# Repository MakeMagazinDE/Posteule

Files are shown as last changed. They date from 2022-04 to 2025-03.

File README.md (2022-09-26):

GitHub Logo

Maker Media GmbH
*** 

# Die animatronische Posteule

### Wie durch Zauberhand: Der Raspberry Pi verwandelt eine Plüscheule in eure persönliche kleine Mitteilungszentrale. Sie flattert, schnattert, blinzelt und kann ihren Kopf drehen. Und das beste: Ihr habt dank Python die Programmierung selbst in der Hand. 

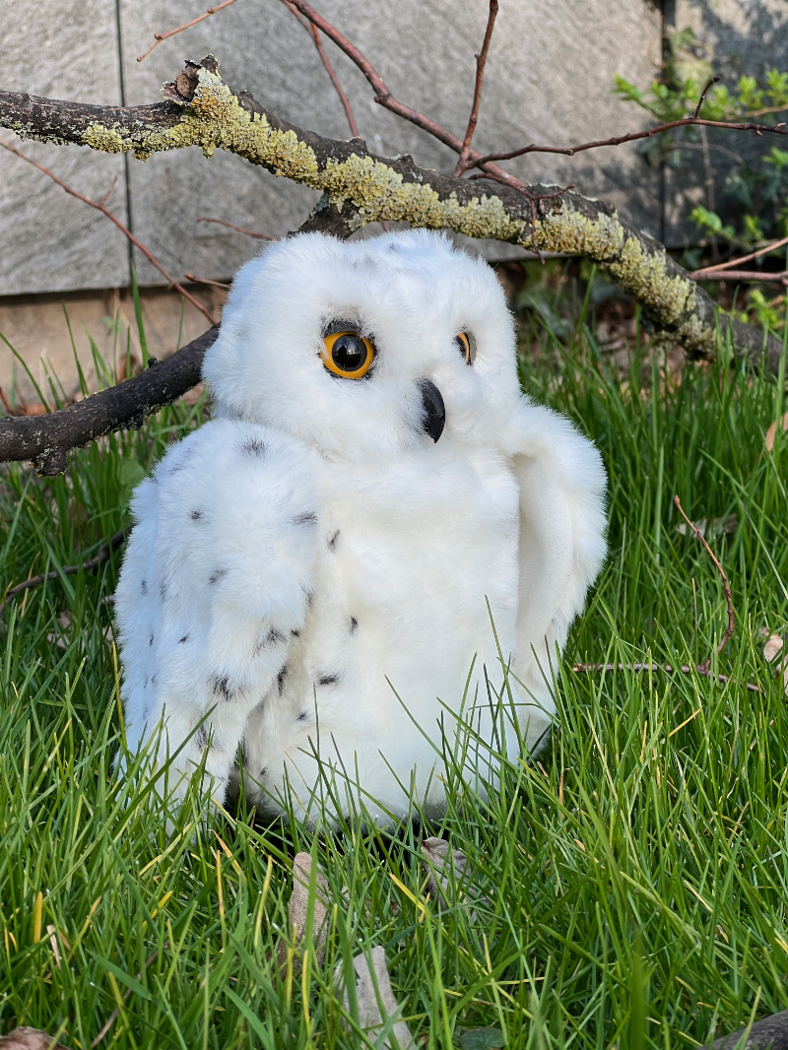
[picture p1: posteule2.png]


Hier findet ihr die benötigten Dateien für den 3D-Druck und die Skripts für die Programmierung. <br>Die 3D-Dateien sind bereits ausgerichtet und mit Cura getestet. 

### Verwendete Druckparameter:
<b>Material:</b> PLA <br>
<b>Temp.:</b> 210°C <br>
<b>Infill:</b> 25% <br>
<b>Support:</b> überall, Zickzack <br>
<b>Schichthöhe:</b> 0,2mm (0,1mm für K5, K6 und K7) <br>
<b>Druckgeschwindigkeit:</b> 50mm/s (20mm/s für K5, B1 und B2) <br>
<b>Bewegungsgeschwindigkeit:</b> 100mm/s (50mm/s für K5, B1 und B2) <br>
<b>Druckplattenhaftung:</b> Skirt (Brim für K5, B1 und B2) <br>
<br>
### Hinweise: 
### Zur E-Mail-Abfrage:
- Verwendet für die Eule eine gesonderte E-Mail-Adresse, weil die Funktion checkIncoming() nach dem Abfragen alle E-Mails löscht.
### Zu den 3D-Dateien aus Teil 1:
- Das Augenlid <b>K5</b> muss zweimal gedruckt werden, die Ringe <b>F1</b> dreimal. <br>
### Zu den 3D-Dateien aus Teil 2:
- Folgende Dateien müssen zweimal gedruckt werden: <b>A8, A9, BN1, BN3, FX</b> und <b>G4</b>
### Zu optimierten 3D-Dateien:
- Es gibt ein paar angepasste 3D-Druckdaten zu <a href="https://github.com/MakeMagazinDE/Posteule/tree/main/3D-Druck/Teil%201/Optimierte%20Modelle"><b>Teil 1</b></a> und <a href="https://github.com/MakeMagazinDE/Posteule/tree/main/3D-Druck/Teil%202/Optimierte%20Modelle"><b>Teil 2</b></a>.
### Die Grafiken 7 und 10 aus der zweiten Bauanleitung (Make 2/22) wurden mit Ziffern ergänzt:
- Ihr findet sie in dem Ordner <a href="https://github.com/MakeMagazinDE/Posteule/tree/main/Extras"><b>Extras</b></a>.

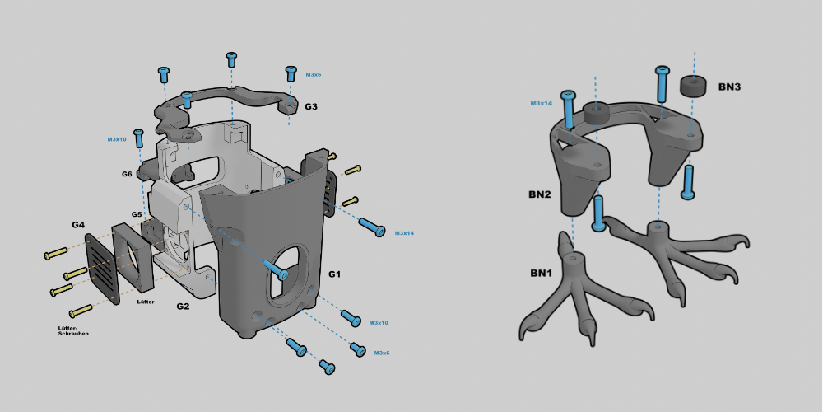
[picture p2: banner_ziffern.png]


<br>

### Hinweis zu dem Servo, der den Augenmechanismus steuert:
Die Bauform der MG90s-Servos scheint sich je nach Hersteller zu unterscheiden. Dadurch kann es passieren, dass der Arm <b>A2</b> mit <b>K1</b> kollidiert, wenn die Welle zu kurz ist oder zu weit hinten sitzt. Zwischen <b>A2</b> und <b>K1</b> sollte eine ca. 0,6mm große Lücke vorhanden sein, damit sich der Arm am Servo problemlos bewegen kann. Haltet am besten den Arm <b>A2</b> einmal an den Servo, und schaut von oben, ob ihr eine Lücke seht. <br>In dem Ordner <a href="https://github.com/MakeMagazinDE/Posteule/tree/main/3D-Druck/Teil%202/Extra"><b>3D-Druck/Teil 2/Extra</b></a> findet ihr die Datei <b>servo_spacer.stl</b>. Dabei handelt es sich um einen kleinen Ring, der in den Arm <b>A2</b> eingesetzt werden kann, bevor ihr ihn am Servo montiert. Er ist 1mm hoch, damit ihr ihn in eurem Slicer auf die richtige Größe (Z-Achse) skalieren könnt. Für alle, die bereits die Teile für den zweiten Artikel gedruckt haben: Der Abstandhalter kann auch aus Pappe gefertigt werden. In der Kurzinfo zum zweiten Artikel findet ihr den Link zu einem Video, das näher darauf eingeht.
<br>
<br>
### Befehle, die nach der Installation von Raspberry Pi OS eingegeben werden müssen <br>(siehe Teil 2 der Bauanleitung):
sudo apt update <br>
sudo apt full-upgrade <br>
sudo apt install python3-pip <br>
sudo apt install ffmpeg libavcodec-extra <br>
sudo apt install i2c-tools <br>
sudo apt install libportaudio2 <br>
sudo pip3 install imapclient <br>
sudo pip3 install smbus <br>
sudo pip3 install adafruit-circuitpython-lis3dh <br>
sudo pip3 install adafruit-circuitpython-servokit <br>
sudo pip3 install pysinewave <br>
sudo pip3 install pydub <br>

<br><br>
Den vollständigen Artikel für den <b>ersten Teil</b> der Bauanleitung gibt es in der [Make-Ausgabe 1/2022](https://www.heise.de/select/make/2022/1/2135511401796522217) zu lesen. 
<br>
Den vollständigen Artikel für den <b>zweiten Teil</b> der Bauanleitung gibt es in der [Make-Ausgabe 2/2022](https://www.heise.de/select/make/2022/2/2203916022634105772) zu lesen.

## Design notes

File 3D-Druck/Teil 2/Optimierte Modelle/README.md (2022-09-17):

In diesem Ordner befinden sich optimierte Druck-Dateien.

- <b>G2_ver2.stl</b> hat kleinere Durchgangslöcher. Ihr Durchmesser wurde von 3mm auf 2,8mm verkleinert.

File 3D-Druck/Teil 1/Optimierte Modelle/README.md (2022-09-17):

In diesem Ordner befinden sich optimierte Druck-Dateien.

- <b>N1_ver2.stl</b> benötigt keine Stützkonstruktion mehr für den 3D-Druck und verfügt über ein zusätzliches Loch, um mit <b>N2</b> verbunden zu werden.
- <b>N2_ver2.stl</b> benötigt keine Stützkonstruktion mehr für den 3D-Druck.
- <b>V1_ver2.stl</b> hat engere Löcher an den Stellen, an denen die Servos angeschraubt werden.

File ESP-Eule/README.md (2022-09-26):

GitHub Logo

Maker Media GmbH
*** 

# Die animatronische Posteule - ESP-Version

### Ob mit Plüsch oder ohne: Die animatronische Posteule aus der Make 1/22 und 2/22 läuft jetzt auch mit einem ESP32 und dem YX5300-MP3-Player. Kein Problem also, wenn ihr keinen Raspberry Pi zur Hand habt. 

Hier findet ihr die benötigten Dateien für den 3D-Druck und die Skripts für die Programmierung mit der Arduino-IDE. 

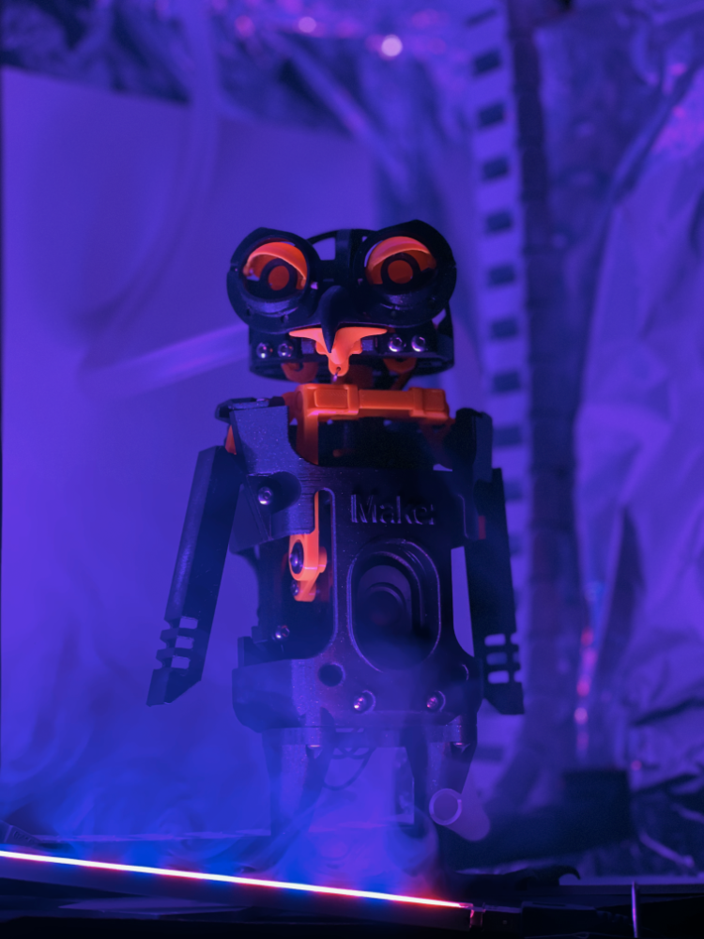
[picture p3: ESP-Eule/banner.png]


### Hinweise: 
- Ihr benötigt zusätzlich die Bauteile und Anleitungen aus der Make 1/22 und 2/22.
- Verwendet für die Eule eine gesonderte E-Mail-Adresse, weil die Funktion checkIncoming() nach dem Abfragen alle E-Mails löscht.

<br>

Den <b>ergänzenden Artikel</b> für den ESP-Umbau gibt es in der [Make-Ausgabe 5/22](https://www.heise.de/select/make/2022/5/2220807460904208992) zu lesen.
<br>
Den vollständigen Artikel für den <b>ersten Teil</b> der Bauanleitung gibt es in der [Make-Ausgabe 1/22](https://www.heise.de/select/make/2022/1/2135511401796522217) zu lesen. 
<br>
Den vollständigen Artikel für den <b>zweiten Teil</b> der Bauanleitung gibt es in der [Make-Ausgabe 2/22](https://www.heise.de/select/make/2022/2/2203916022634105772) zu lesen.

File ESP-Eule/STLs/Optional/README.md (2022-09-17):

Dieser Ordner beinhaltet optionale 3D-Modelle für die Variante der <b>[Make 5/22](https://www.heise.de/select/make/2022/5/2220807460904208992)</b>, die auch auf der <b>[Maker Faire 2022](https://maker-faire.de)</b> zu sehen war. Die ESP-Posteule lässt sich allerdings auch in der Plüsch-Variante bauen. Dafür benötigt ihr die 3D-Daten aus dem ersten und zweiten Teil der Anleitung.

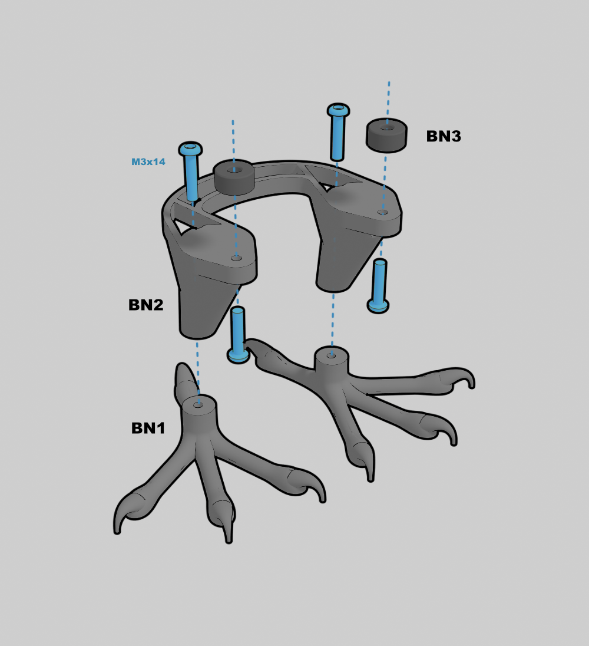
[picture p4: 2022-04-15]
Extras/posteule_grafik10_beziffert.png

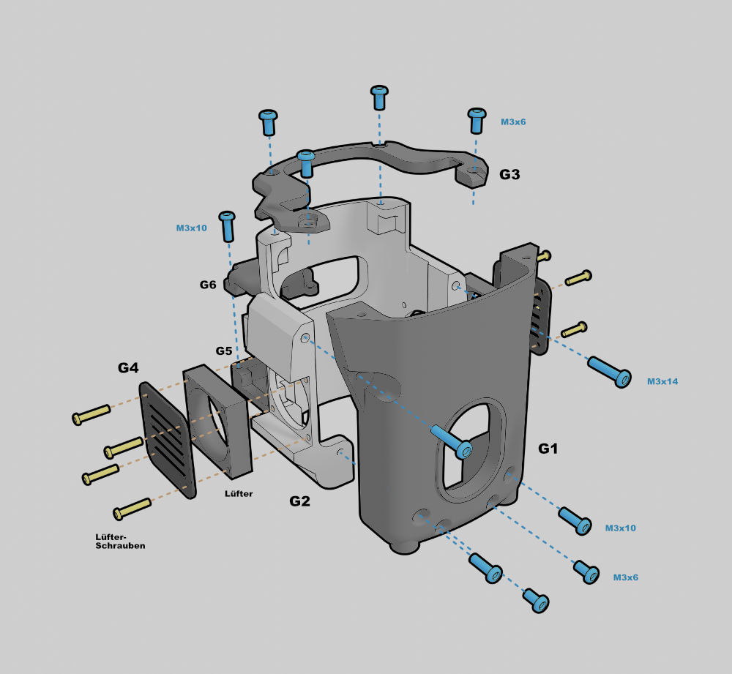
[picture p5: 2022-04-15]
Extras/posteule_grafik7_beziffert.png

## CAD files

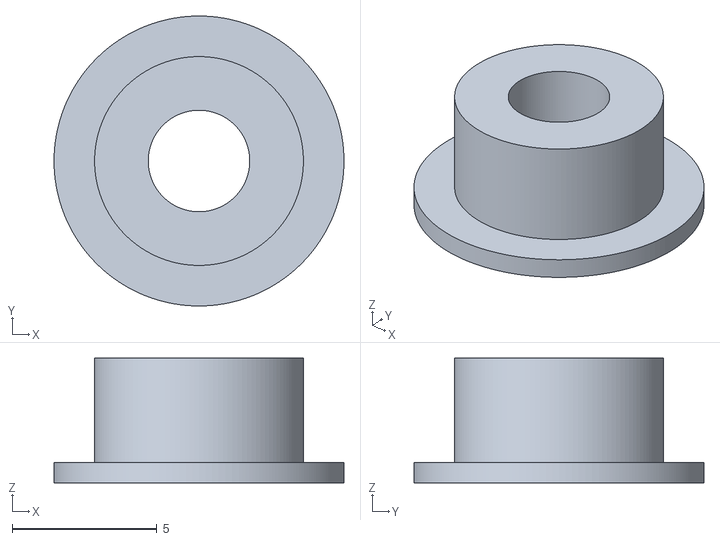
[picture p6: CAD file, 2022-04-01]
3D-Druck/Teil 1/B4.stl
10.0 x 10.0 x 4.30

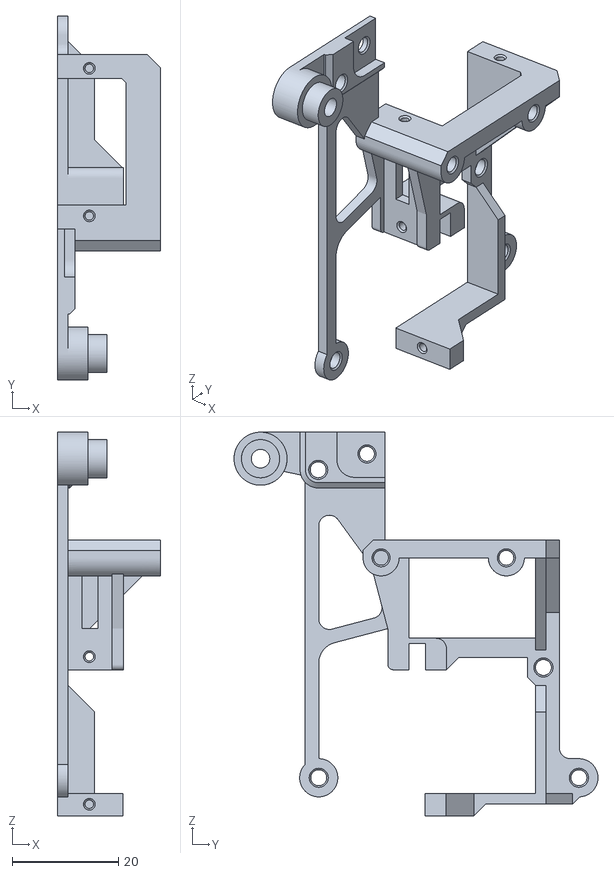
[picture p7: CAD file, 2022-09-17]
3D-Druck/Teil 1/Optimierte Modelle/V1_ver2.stl
19.4 x 68.6 x 72.3

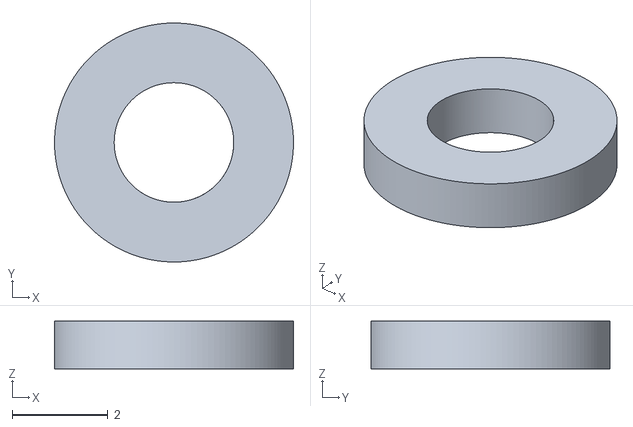
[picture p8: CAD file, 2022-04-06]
3D-Druck/Teil 2/Extra/servo_spacer.stl
5.00 x 5.00 x 1.00

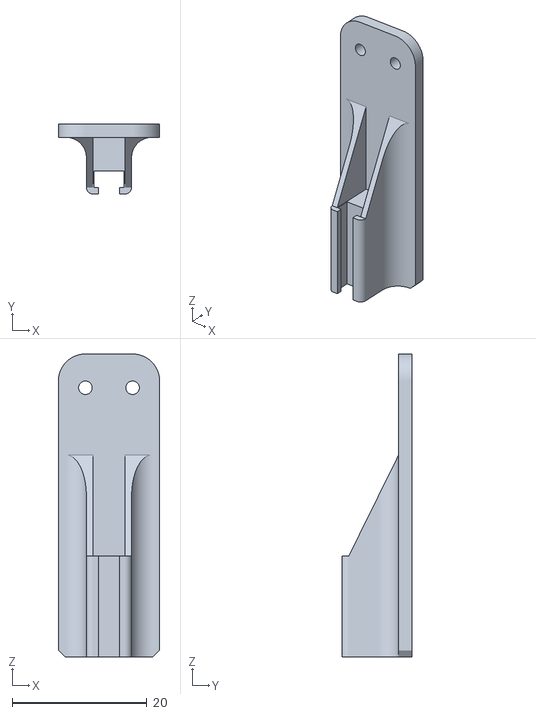
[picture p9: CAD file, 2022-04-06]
3D-Druck/Teil 2/FX.stl
15.0 x 10.4 x 44.9

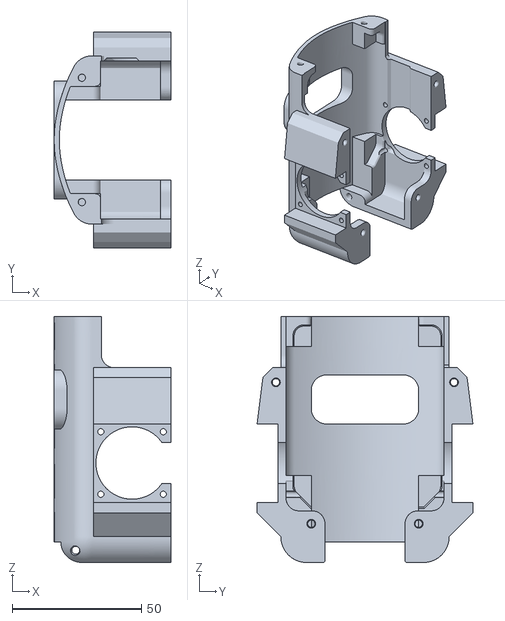
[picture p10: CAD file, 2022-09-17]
3D-Druck/Teil 2/Optimierte Modelle/G2_ver2.stl
45.2 x 83.6 x 95.3

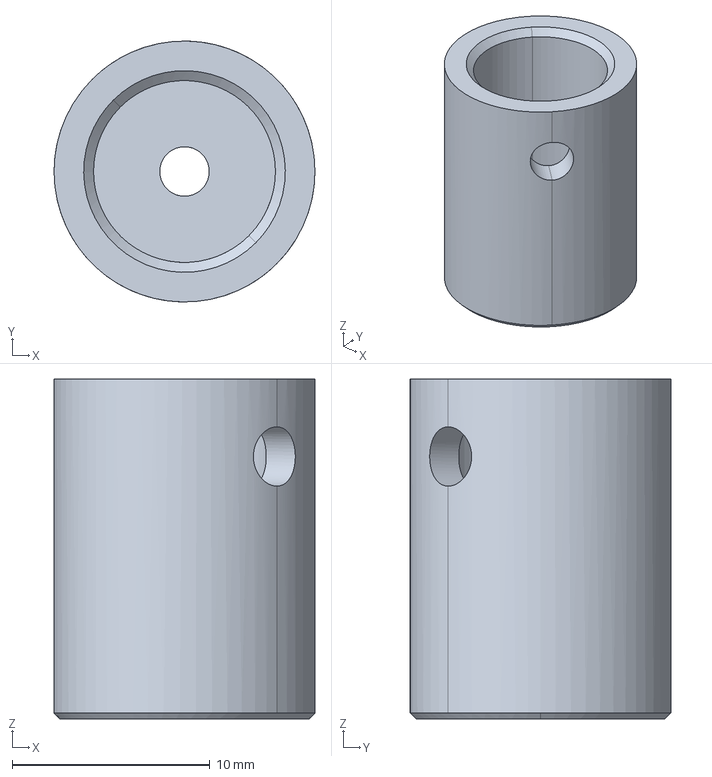
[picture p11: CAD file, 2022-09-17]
ESP-Eule/Servoverbinder-CAD/N2.stp
13.2 x 13.2 x 17.2 mm

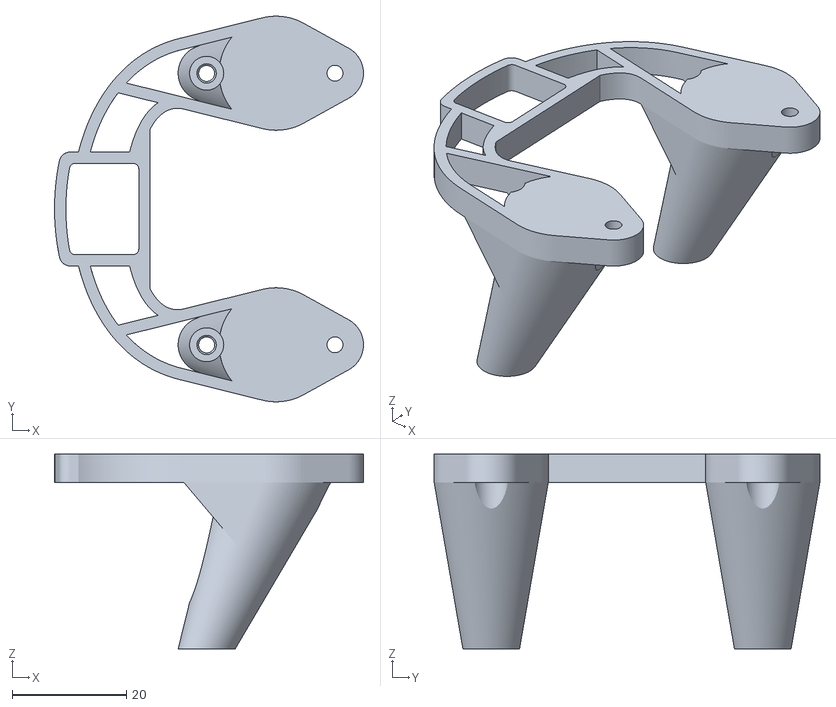
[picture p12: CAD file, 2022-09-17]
ESP-Eule/STLs/Essentials/BN2E.stl
54.2 x 67.6 x 34.2

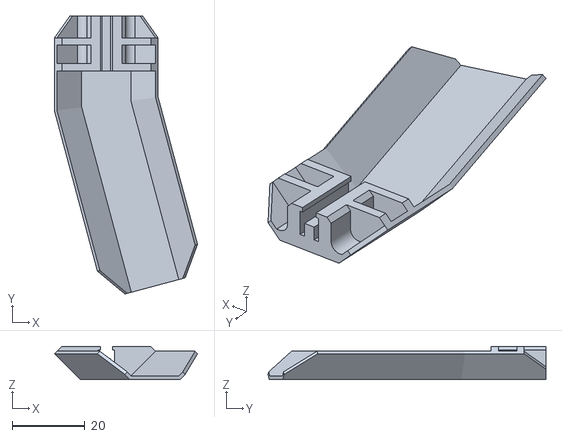
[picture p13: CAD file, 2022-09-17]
ESP-Eule/STLs/Optional/FXE_rechts.stl
39.3 x 76.2 x 9.10

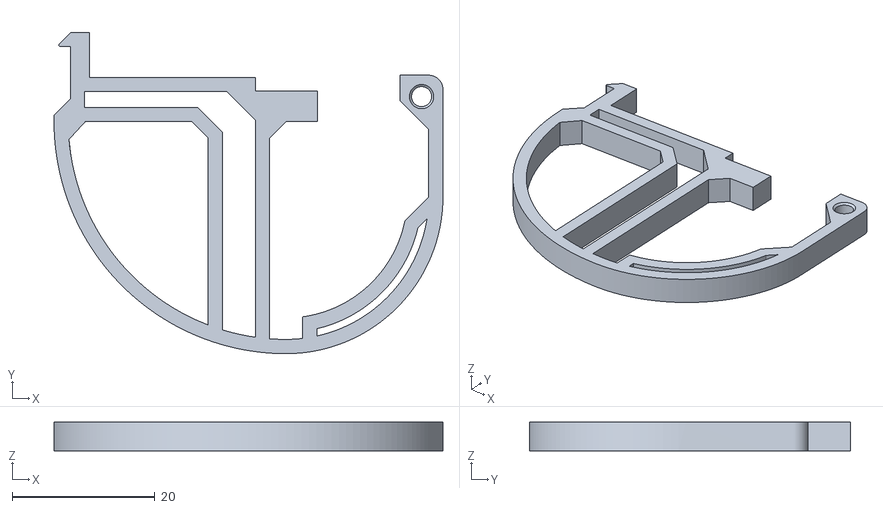
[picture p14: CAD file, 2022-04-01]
3D-Druck/Teil 1/K3.stl
54.5 x 45.0 x 4.00

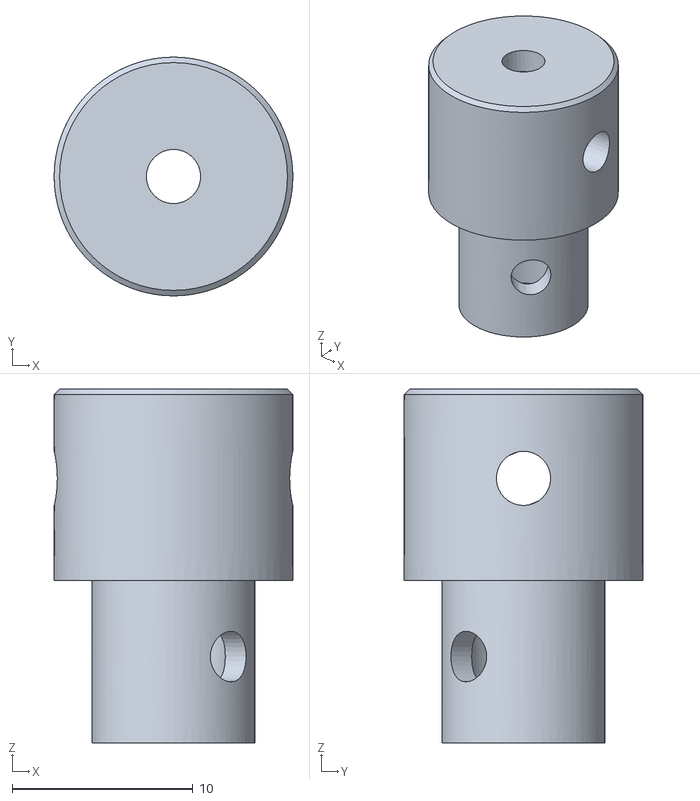
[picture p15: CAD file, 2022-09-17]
3D-Druck/Teil 1/Optimierte Modelle/N1_ver2.stl
13.2 x 13.2 x 19.6

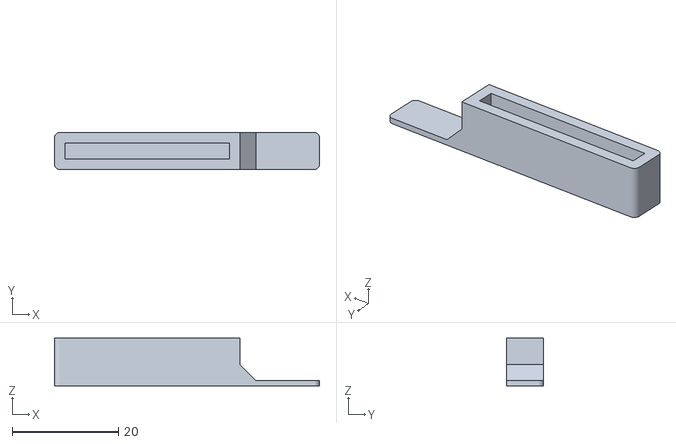
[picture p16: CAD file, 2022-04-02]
3D-Druck/Teil 2/gpio_cap.stl
50.0 x 7.00 x 9.00

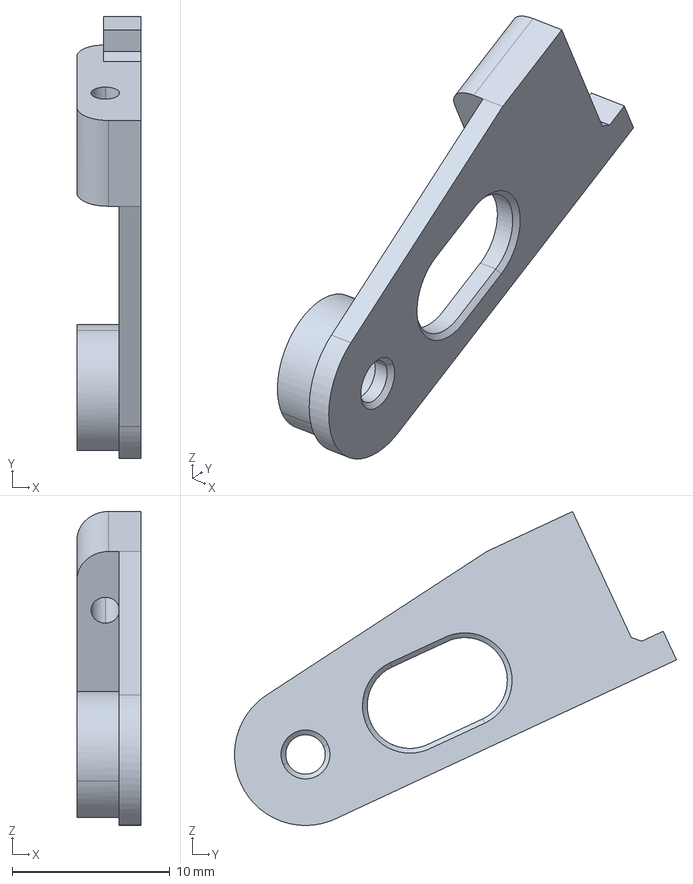
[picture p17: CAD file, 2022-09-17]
ESP-Eule/Servoverbinder-CAD/A2.stp
4.07 x 28.0 x 19.9 mm

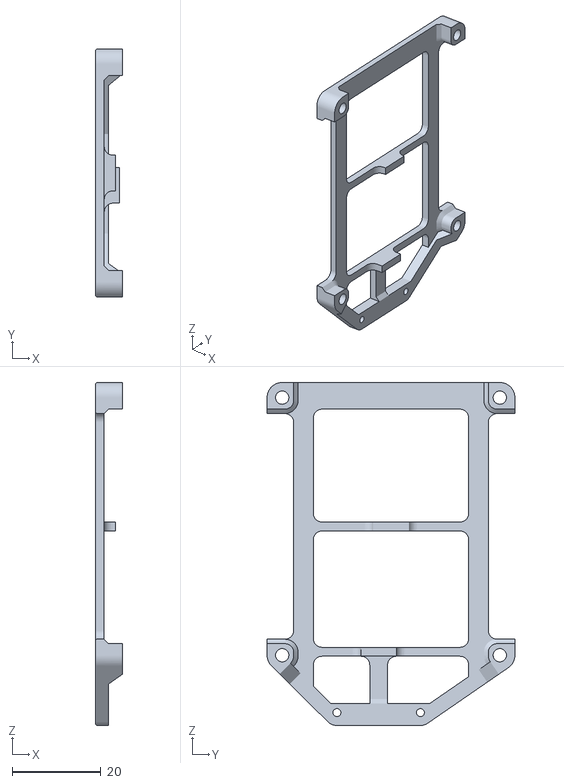
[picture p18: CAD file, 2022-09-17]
ESP-Eule/STLs/Essentials/R1E.stl
6.16 x 55.8 x 77.2

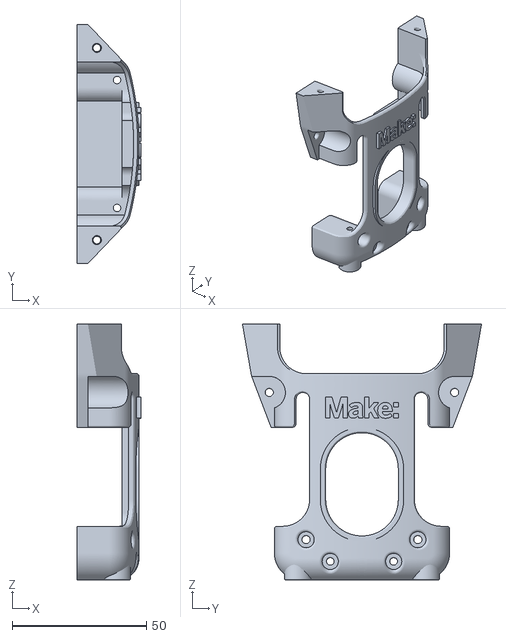
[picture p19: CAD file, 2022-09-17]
ESP-Eule/STLs/Optional/G1_cyber.stl
23.7 x 89.0 x 95.3

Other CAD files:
3D-Druck/Teil 1/Optimierte Modelle/N2_ver2.stl
3D-Druck/Teil 1/RF1.stl
3D-Druck/Teil 2/A9.stl
ESP-Eule/Servoverbinder-CAD/B5.stp
3D-Druck/Teil 1/B1.stl
3D-Druck/Teil 1/B2.stl
3D-Druck/Teil 1/B3.stl
3D-Druck/Teil 1/B5.stl
3D-Druck/Teil 1/B6.stl
3D-Druck/Teil 1/F1.stl
3D-Druck/Teil 1/K1.stl
3D-Druck/Teil 1/K2.stl
3D-Druck/Teil 1/K4_L.stl
3D-Druck/Teil 1/K4_R.stl
3D-Druck/Teil 1/K6.stl
3D-Druck/Teil 1/K7.stl
3D-Druck/Teil 1/K8.stl
3D-Druck/Teil 1/K9_L.stl
3D-Druck/Teil 1/K9_R.stl
3D-Druck/Teil 1/LF1.stl
3D-Druck/Teil 1/LF2.stl
3D-Druck/Teil 1/N1.stl
3D-Druck/Teil 1/N2.stl
3D-Druck/Teil 1/R1.stl
3D-Druck/Teil 1/R2.stl
3D-Druck/Teil 1/V1.stl
3D-Druck/Teil 1/V2.stl
3D-Druck/Teil 1/V3.stl
3D-Druck/Teil 1/V4.stl
3D-Druck/Teil 1/V5.stl
3D-Druck/Teil 2/A1.stl
3D-Druck/Teil 2/A2.stl
3D-Druck/Teil 2/A3.stl
3D-Druck/Teil 2/A4.stl
3D-Druck/Teil 2/A5.stl
3D-Druck/Teil 2/A6.stl
3D-Druck/Teil 2/A7.stl
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

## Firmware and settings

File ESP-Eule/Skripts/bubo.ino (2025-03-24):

#include <Wire.h>
#include <Adafruit_PWMServoDriver.h>

#include <WiFi.h>
#include <ESP_Mail_Client.h>


/**********************/
/* WLAN-EINSTELLUNGEN */
/**********************/

#define WIFI_SSID "hier SSID eintragen"
#define WIFI_PASSWORD "hier Passwort eintragen"


/************************/
/* E-MAIL-EINSTELLUNGEN */
/************************/

#define IMAP_HOST "imap.gmail.com"
#define IMAP_PORT 993
#define AUTHOR_EMAIL "emailAdresse@gmail.com"
#define AUTHOR_PASSWORD "App-Passwort hier eintragen"

IMAPSession imap;
ESP_Mail_Session session;
IMAP_Config config;
#define checkFreq 60000  //Einmal pro Minute E-Mails abrufen


/***********************/
/* AUDIO-EINSTELLUNGEN */
/***********************/

//Das Array für die serielle Kommunikation zwischen ESP32 und YX5300
static int8_t commandArray[8] = {0x7E,0xFF,0x06,0,0x00,0,0,0xEF};

//Konstanten für die Befehle, die wir benötigen. Weitere gibt es im Handbuch des YX5300.
#define sndPlayFolderFile 0X0F
#define sndSelectDevice 0X09
#define sndDevTF 0X02
#define sndSetVolume 0X06

//Sounds definieren, damit man sich nicht die Namen merken muss.
#define startUp 1
#define owlHoot 2


/***********************/
/* SERVO-EINSTELLUNGEN */
/***********************/

Adafruit_PWMServoDriver pwm = Adafruit_PWMServoDriver(0x40);  //I2C 

#define minPulseWidth 600
#define maxPulseWidth 2400
#define freq 50
#define servoEyes 0   //Servo für die Augen steckt im ersten Slot
#define servoBeak 1   //Servo für den Schnabel steckt im zweiten Slot
#define servoHead 2   //Servo für den Nacken steckt im dritten Slot
#define servoWings 3  //Servo für die Flügel steckt im vierten Slot

#define eyesMin 90    
#define eyesMax 90    

#define beakMin 90    
#define beakMax 90    

#define headMin 0
#define headMid 90 
#define headMax 180    

#define wingsMin 90  
#define wingsMax 90  

//aktuelle Servo-Positionen festlegen
int eyesPos = eyesMin;  
int beakPos = beakMin;
int headPos = headMid;
int wingsPos = wingsMax;

//PWM in Winkel umrechnen
int servoAngle(int angle){

  int pulseWidth, analogValue;

  //Die Pulsweite (600-2400) wird auf die Winkel (0-180) gemappt.
  pulseWidth = map(angle, 0, 180, minPulseWidth, maxPulseWidth);
  //Danach wird daraus ein 12-Bit Wert für den Winkel errechnet.
  analogValue = int(float(pulseWidth)/1000000 * freq * 4096);
  return analogValue;
  
}


/************************/
/* GENERELLE FUNKTIONEN */
/************************/

//Diese Funktion fügt die Funktion und ihre Parameter in den commandArray ein
//und sendet den Befehl seriell an den YX5300-MP3-Player.
void esp2mp3(byte func, byte param1, byte param2){

  commandArray[3] = func;
  commandArray[5] = param1;
  commandArray[6] = param2;

  for(uint8_t i=0; i<8; i++){
    Serial2.write(commandArray[i]);
  }
}


//Servos auf die Ausgangspositionen einstellen
void servoStartUpReset() {

  pwm.setPWM(servoEyes, 0, servoAngle(eyesPos));
  pwm.setPWM(servoBeak, 0, servoAngle(beakPos));
  pwm.setPWM(servoHead, 0, servoAngle(headPos));
  pwm.setPWM(servoWings, 0, servoAngle(wingsPos));
  Serial.println("Alle Servos in Position.");

}


//Diese Funktion verbindet den ESP mit dem WLAN.
void connectWiFi(){
  
  WiFi.begin(WIFI_SSID, WIFI_PASSWORD);
  while (WiFi.status() != WL_CONNECTED){
    Serial.print(".");
    delay(200);
  }
  //Serial.println();
  //Serial.print("Zum WLAN-Netzwerk ");
  //Serial.print(WIFI_SSID);
  //Serial.println(" verbunden.");
  //Serial.print("IP-Adresse: ");
  //Serial.println(WiFi.localIP());
  //Serial.println();
}


//Die Hauptfunktion, die E-Mails abruft, löscht und Bewegungen ausführt.
void checkIncoming(){

  // Session config
  session.server.host_name = IMAP_HOST;
  session.server.port = IMAP_PORT;
  session.login.email = AUTHOR_EMAIL;
  session.login.password = AUTHOR_PASSWORD;

  // In die Klasse MessageList kommen alle E-Mails, die gelöscht werden sollen.
  MessageList toDelete;
  
  if (!imap.connect(&session, &config))
    return;
  
  imap.selectFolder("INBOX");

  SelectedFolderInfo sFolder = imap.selectedFolder();
  ESP_MAIL_PRINTF("Total Message Index: %d\n", sFolder.msgCount());
  ESP_MAIL_PRINTF("Unseen Message Index: %d\n", sFolder.unseenIndex());

  //Wenn eine Nachricht im Posteingang ist, wird etwas ausgeführt.
  if (imap.selectedFolder().msgCount() > 0){
    owlMF();

    /* Hier können auch andere Abläufe erstellt werden. Ich finde es aber übersichtlicher,
     *  sie in eigene Funktionen wie owlMF() zu verpacken.
     */
    //eyesBlink();
    //wingsUp(50);
  }

  //Alle Nachrichten im Posteingang werden gelöscht.
  for(int i = imap.selectedFolder().msgCount(); i > 0; i--){
    toDelete.add(imap.getUID(i));
  }
  
  imap.deleteMessages(&toDelete, true);

  //Nach der Pause checkFreq wird der Posteingang erneut abgefragt.
  delay(checkFreq);
  
}



/***************************/
/* GRUNDLEGENDE BEWEGUNGEN */
/***************************/

/* FLÜGEL HOCH */
void wingsUp(int aniSpeed) {

  if (wingsPos>=wingsMax){
    for (int i=wingsPos; i>=wingsMax; i--){
      pwm.setPWM(servoWings, 0, servoAngle(i));
      delay(aniSpeed);
      Serial.println(i);
    }
    wingsPos = wingsMax;
    Serial.println("Wings Position");
    Serial.println(wingsPos);
    pwm.setPWM(servoWings, 0, 4096);
  }
  
}

/* FLÜGEL RUNTER */
void wingsDown(int aniSpeed) {

  if (wingsPos<=wingsMin){
    for (int i=wingsPos; i<=wingsMin; i++){
      pwm.setPWM(servoWings, 0, servoAngle(i));
      delay(aniSpeed);
    }
    wingsPos = wingsMin;
    Serial.println("Wings Position");
    Serial.println(wingsPos);
    pwm.setPWM(servoWings, 0, 4096);
  }

}

/* AUGEN AUF */
void eyesOpen(int aniSpeed) {
  
  if (eyesPos>=eyesMin){
    for (int i=eyesPos; i>=eyesMin; i--){
      pwm.setPWM(servoEyes, 0, servoAngle(i));
      delay(aniSpeed);
    }
    eyesPos = eyesMin;
    Serial.println("Eyes Position");
    Serial.println(eyesPos);
    pwm.setPWM(servoEyes, 0, 4096);
  }
}


/* AUGEN ZU */
void eyesShut(int aniSpeed) {
  
  if (eyesPos<=eyesMax){
    for (int i=eyesPos; i<=eyesMax; i++){
      pwm.setPWM(servoEyes, 0, servoAngle(i));
      delay(aniSpeed);
    }
    eyesPos = eyesMax;
    Serial.println("Eyes Position");
    Serial.println(eyesPos);
    pwm.setPWM(servoEyes, 0, 4096);
  }
}


/* BLINZELN
 * Die Funktion eyesBlink() hat keine Variable aniSpeed, weil das Blinzeln 
 * mit maximaler Geschwindigkeit ablaufen soll. Man könnte aber, wie bei den 
 * anderen Funktionen noch aniSpeed noch ergänzen.
*/
void eyesBlink(){
  
  pwm.setPWM(servoEyes, 0, servoAngle(eyesMin));
  delay(100);
  pwm.setPWM(servoEyes, 0, servoAngle(eyesMax));
  delay(100);
  pwm.setPWM(servoEyes, 0, servoAngle(eyesMin));
  delay(100);
  pwm.setPWM(servoEyes, 0, 4096);
}


/* SCHNABEL AUF */
void beakOpen(int aniSpeed) {
  
  if (beakPos<=beakMax){
    for (int i=beakPos; i<=beakMax; i++){
      pwm.setPWM(servoBeak, 0, servoAngle(i));
      delay(aniSpeed);
    }
    beakPos = beakMax;
    Serial.println("Beak Position");
    Serial.println(beakPos);
    pwm.setPWM(servoBeak, 0, 4096);
  }
}


/* SCHNABEL ZU */
void beakClose(int aniSpeed) {
  
  if (beakPos>beakMin){
    for (int i=beakPos; i>=beakMin; i--){
      pwm.setPWM(servoBeak, 0, servoAngle(i));
      delay(aniSpeed);
    }
    beakPos = beakMin;
    Serial.println("Beak Position");
    Serial.println(beakPos);
    pwm.setPWM(servoBeak, 0, 4096);
  }
}

/* KOPF NACH RECHTS DREHEN */
void headRight(int aniSpeed) {
  
  if (headPos>=headMin){
    for (int i=headPos; i>=headMin; i--){
      pwm.setPWM(servoHead, 0, servoAngle(i));
      delay(aniSpeed);
    }
    headPos = headMin;
    Serial.println("Head Position");
    Serial.println(headPos);
    pwm.setPWM(servoHead, 0, 4096);
  }
}

/* DEN KOPF NACH LINKS DREHEN */
void headLeft(int aniSpeed) {
    
  if (headPos<=headMax){
    for (int i=headPos; i<=headMax; i++){
      pwm.setPWM(servoHead, 0, servoAngle(i));
      delay(aniSpeed);
    }
    headPos = headMax;
    Serial.println("Head Position");
    Serial.println(headPos);
    pwm.setPWM(servoHead, 0, 4096);
  }
}

/*DEN KOPF ZUR MITTE DREHEN */
void headCenter(int aniSpeed) {
    
  if (headPos<=headMid){
    for (int i=headPos; i<=headMid; i++){
      pwm.setPWM(servoHead, 0, servoAngle(i));
      delay(aniSpeed);
    } 
    headPos = headMid;
    Serial.println("Head Position");
    Serial.println(headPos);
    pwm.setPWM(servoHead, 0, 4096);
    
  } else if (headPos>=headMid){
    for (int i=headPos; i>=headMid; i--){
      pwm.setPWM(servoHead, 0, servoAngle(i));
      delay(aniSpeed);
    }
    headPos = headMid;
    Serial.println("Head Position");
    Serial.println(headPos);
    pwm.setPWM(servoHead, 0, 4096);
  }
}


/* DEN KOPF ZU EINEM ZUFÄLLIGEN WINKEL DREHEN */
void headRand(int aniSpeed) {

  int randAngle = random(headMin+5, headMax-5);

  if (headPos<=randAngle){
    for (int i=headPos; i<=randAngle; i++){
      pwm.setPWM(servoHead, 0, servoAngle(i));
      delay(aniSpeed);
    }
    headPos = randAngle;
    Serial.println("Head Position");
    Serial.println(headPos);
    pwm.setPWM(servoHead, 0, 4096);

  } else if (headPos>=randAngle){
    for (int i=headPos; i>=randAngle; i--){
      pwm.setPWM(servoHead, 0, servoAngle(i));
      delay(aniSpeed);
    }
    headPos = randAngle;
    Serial.println("Head Position");
    Serial.println(headPos);
    pwm.setPWM(servoHead, 0, 4096);
  }
}



/*********************************/
/* ANIMATIONEN UND CHOREOGRAFIEN */
/*********************************/

/* BEWEGUNGSABLAUF DER MAKER FAIRE 2022
 *  Ihr könnt so auch eigene Bewegungsabläufe schaffen.
 *  Im void loop() wird lediglich owlMF() aufgerufen
 *  und spielt die darin enthaltenen Bewegungen ab.
 */
void owlMF(){

  eyesOpen(20);
  delay(1000);
  eyesBlink();  //Hier keinen Wert in die Klammer eintragen, da eyesBlink() keine Variable aniSpeed hat.
  delay(random(1000,2000));
  headRand(random(5,20));
  delay(random(1000,3000));

  //Zufällige Flügelbewegung
  int flap = random(0,2);
  if (flap==1){
    wingsUp(random(5,20));
    delay(random(0,2000));
    wingsDown(random(5,20));
    delay(random(1000,2000));
    eyesBlink();
  }

  //Zufällige Schnabelbewegung
  int chatter = random(0,2);
  if (chatter==1){
    beakOpen(random(5,20));
    delay(random(0,2000));
    beakClose(random(5,20));
    delay(random(1000,2000));
    eyesBlink();
  }

  //Zufällig schlafen
  int sleeping = random(0,2);
  if (sleeping==1){
    delay(2000);
    beakOpen(20);
    eyesShut(20);
    beakClose(30);
    delay(random(3000,20000));
    eyesOpen(20);
    delay(random(1000,2000));
    eyesBlink();
  }

  //Zufällige Animation
  int widerstand = random(0,3);
  if (widerstand==1){
    beakOpen(random(5,20));
    delay(1000);
    esp2mp3(sndPlayFolderFile, 1, 3);
    delay(2000);
    beakClose(random(5,20));
    delay(random(1000,2000));
    eyesBlink();
  }
  
}




//Eine kleiner Animationsablauf
void animation1(){

  wingsUp(50);
  delay(2000);
  wingsDown(50);
  delay(2000);
  
}

//Eine kleiner Animationsablauf
void animation2(){

  headLeft(30);
  delay(1000);
  headRight(30);
  delay(1000);
  headCenter(100);
  delay(2000);
  
}

//Eine kleiner Animationsablauf
void animation3(){

  eyesOpen(10);
  beakOpen(10);
  esp2mp3(sndPlayFolderFile, 1, 3);
  delay(3000);   //Zeit für den Sound, um zu Ende zu spielen
  beakClose(30);
  eyesShut(100);
  
}

//Diese Funktion spielt zufällig einen der kleinen Animationsabläufe ab
void randAnimation(){

  int whichAnimation = random(0,3);
  if (whichAnimation==0){
    animation1();
  } else if (whichAnimation==1){
    animation2();
  } else if (whichAnimation==2){
    animation3();
  } 
}



/*****************************************/
/* HIER STARTET DAS EIGENTLICHE PROGRAMM */
/*****************************************/

void setup() {

  //Serielle Verbindung zum PC
  Serial.begin(115200);

  //Mit dem WLAN verbinden
  connectWiFi();

  //Servo PWM starten
  pwm.begin();
  pwm.setPWMFreq(freq);

  //Verbindung zum YX5300 herstellen
  Serial2.begin(9600, SERIAL_8N1, 16, 17);
  esp2mp3(sndSelectDevice, 0, sndDevTF);
  delay(200);

  //Lautstärke einstellen 0xD2 = 210 (ca. X Prozent)
  esp2mp3(sndSetVolume, 0, 0xD2);
  delay(200);

  //StartUp-Sound abspielen
  esp2mp3(sndPlayFolderFile, 1, 1);
  delay(3000);

  //Alle Servos auf Mittelstellung setzen
  servoStartUpReset();
  
}

void loop() {

  checkIncoming();

}

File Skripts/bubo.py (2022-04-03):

#!/usr/bin/python3

import time
import random
from adafruit_servokit import ServoKit
from time import sleep
from imapclient import IMAPClient
from pydub import AudioSegment
from pydub.playback import play


###########################
### Variablen festlegen ###
###########################

### Variablen fuer den E-Mail-Abruf

HOSTNAME = 'imap.gmail.com'  #oder Hostname eines anderen Anbieters
USERNAME = 'mail@gmail.com' #gebt hier die Gmail-Adresse ein
PASSWORD = 'katze123' #und hier das App-Passwort

#Die Mail-Abfrage in Sekunden. Wenn der Wert zu niedrig ist, kann euch der Mail-
#Server blockieren, also übertreibt es nicht. 5 Sekunden haben bei mir für Tests
#noch gut funktioniert. Im Betrieb muss die Eule nicht alle paar Sekunden nach-
#sehen.

checkFreq = 20


### Variablen für die Servosteuerung

kit = ServoKit(channels=16)
headMid = 90
headMin = 0
headMax = 180
eyesMin = XX #Minimalwert einsetzen für Augen zu
eyesMax = XX #Maximalwert einsetzen für Augen auf
beakMin = XX #Minimalwert einsetzen für Schnabel zu
beakMax = XX #Maximalwert einsetzen für Schnabel auf
wingsMin = XX #Minimalwert einsetzen für Flügel unten
wingsMax = XX #Maximalwert einsetzen für Flügel oben


### Variablen für die Animationen

headPos = headMid
headAim = headMid
eyesPos = eyesMin
eyesAim = eyesMin
beakPos = beakMin
beakAim = beakMin
wingsPos = wingsMin
wingsAim = wingsMin
aniSpeed = 0.01

### Eulen-Sounds

#Fügt hier eure eigenen Sounds anstatt der angegeben WAVs ein.

sndHoot = AudioSegment.from_wav('owlHoot.wav')
sndHootLong = AudioSegment.from_wav('owlHootLong.wav')
sndCall = AudioSegment.from_wav('owlCall.wav')
sndWakeup = AudioSegment.from_wav('owlWakeup.wav')
#sndSleep = AudioSegment.from_wav('owlSleep.wav')


###########################
### Einzelne Bewegungen ###
###########################



### AUGEN: servo[0]


def aniBlink():

#Die Augen schließen sich, bis sie sich 0.2 Sekunden später wieder öffnen. 
#Dadurch entsteht ein einzelnes Blinzeln.

  kit.servo[0].angle = eyesMin
  time.sleep(0.2)
  kit.servo[0].angle = eyesMax
  time.sleep(1)
  kit.servo[0].angle = None

def aniCloseEyes():

#Die Augen langsam geschlossen.

  global eyesPos

  eyesAim = eyesMin
  while eyesPos != eyesAim:
    if eyesPos <= eyesAim:
      eyesPos += 1
    else:
      eyesPos -= 1

    kit.servo[0].angle = eyesPos
    time.sleep(aniSpeed)

  kit.servo[0].angle = None


def aniOpenEyes():

#Die Augen werden lansgam geöffnet.

  global eyesPos

  eyesAim = eyesMax
  while eyesPos != eyesAim:
    if eyesPos <= eyesAim:
      eyesPos += 1
    else:
      eyesPos -= 1

    kit.servo[0].angle = eyesPos
    time.sleep(aniSpeed)

  kit.servo[0].angle = None



### SCHNABEL: servo[1]


def aniOpenBeak():

#Der Schnabel wird langsam geöffnet.

  global beakPos

  beakAim = beakMax
  while beakPos != beakAim:
    if beakPos <= beakAim:
      beakPos += 1
    else:
      beakPos -= 1

    kit.servo[1].angle = beakPos
    time.sleep(aniSpeed)

  kit.servo[1].angle = None


def aniCloseBeak():

#Der Schnabel wird langsam geschlossen.

  global beakPos

  beakAim = beakMin
  while beakPos != beakAim:
    if beakPos <= beakAim:
      beakPos += 1
    else:
      beakPos -= 1

    kit.servo[1].angle = beakPos
    time.sleep(aniSpeed)

  kit.servo[1].angle = None



### KOPF: servo[2]

def aniHeadRandom():

#Der Kopf bewegt sich zu einer zufälligen Position.

  global headPos

  headAim = random.randint(headMin,headMax)
  while headPos != headAim:
    if headPos <= headAim:
      headPos += 1
    else:
      headPos -= 1

    kit.servo[2].angle = headPos
    time.sleep(aniSpeed)

  kit.servo[2].angle = None


def aniHeadLeft():

#Der Kopf dreht sich nach links.

  global headPos

  headAim = headMin
  while headPos != headAim:
    if headPos <= headAim:
      headPos += 1
    else:
      headPos -= 1

    kit.servo[2].angle = headPos
    time.sleep(aniSpeed)

  kit.servo[2].angle = None


def aniHeadRight():

#Der Kopf dreht sich nach rechts.

  global headPos

  headAim = headMax
  while headPos != headAim:
    if headPos <= headAim:
      headPos += 1
    else:
      headPos -= 1

    kit.servo[2].angle = headPos
    time.sleep(aniSpeed)

  kit.servo[2].angle = None


def aniHeadForward():

#Der Kopf schaut nach vorn

  global headPos

  headAim = headMid
  while headPos != headAim:
    if headPos <= headAim:
      headPos += 1
    else:
      headPos -= 1

    kit.servo[2].angle = headPos
    time.sleep(aniSpeed)

  kit.servo[2].angle = None


### FLÜGEL: servo[3]

def aniFlapUp():

#Die Flügel bewegen sich hoch.
  global wingsPos

  wingsAim = wingsMax
  while wingsPos != wingsAim:
    if wingsPos <= wingsAim:
      wingsPos += 1
    else:
      wingsPos -= 1

    kit.servo[3].angle = wingsPos
    time.sleep(aniSpeed)

  kit.servo[3].angle = None


def aniFlapDown():

#Die Flügel bewegen sich runter.

  global wingsPos

  wingsAim = wingsMin
  while wingsPos != wingsAim:
    if wingsPos <= wingsAim:
      wingsPos += 1
    else:
      wingsPos -= 1

    kit.servo[3].angle = wingsPos
    time.sleep(aniSpeed)

  kit.servo[3].angle = None



#########################
### Bewegungsabläufe ###
#########################

#Mithilfe der einzelnen Bewegungen und Sounds lassen sich hier ganze Bewegungsabläufe
#choreografieren, die sich anschließend mit einem Befehl abrufen lassen.


def aniSpecialMail():

  aniOpenEyes()
  play(sndWakeup)
  aniFlapUp()
  aniOpenBeak()
  play(sndHoot)
  aniBlink()
  aniCloseBeak()
  aniOpenBeak()
  play(sndHoot)
  aniBlink()
  aniCloseBeak()
  aniFlapDown()
  aniHeadRight()
  aniBlink()
  aniHeadLeft()
  aniHeadForward()
  aniBlink()
  aniCloseEyes()
  #play(sndSleep)


def aniSpecialMail2():

  aniOpenEyes()
  aniBlink()
  time.sleep(1)
  aniBlink()
  aniHeadLeft()
  time.sleep(1)
  aniBlink()
  time.sleep(2)
  aniHeadForward()
  time.sleep(1)
  aniBlink()
  time.sleep(2)
  aniHeadLeft()
  time.sleep(1)
  aniFlapUp()
  aniFlapDown()
  aniBlink()
  aniHeadForward()
  time.sleep(1)
  aniOpenBeak()
  play(sndHoot)
  aniCloseBeak()
  aniBlink()
  aniHeadLeft()
  time.sleep(1)
  aniBlink()
  time.sleep(2)
  aniHeadForward()
  aniBlink()
  time.sleep(2)
  aniCloseEyes()

def aniStartUp():

  aniOpenEyes()
  aniBlink()
  time.sleep(1)
  aniHeadLeft()
  aniBlink()
  aniOpenBeak()
  play(sndHoot)
  aniCloseBeak()
  aniHeadForward()
  time.sleep(1)
  aniBlink()
  aniFlapUp()
  aniFlapDown()
  aniBlink()
  aniHeadRight()
  aniOpenBeak()
  play(sndHoot)
  aniCloseBeak()
  aniHeadForward()
  aniBlink()
  time.sleep(1)
  aniCloseEyes()



#######################
### Startfunktionen ###
#######################

### Alles auf 0 setzen

### Servos in Ausgangsposition

def resetServos():

#Nach vorne schauen

  kit.servo[2].angle = headMid
  time.sleep(1)
  kit.servo[2].angle = None

#Schnabel schließen

  kit.servo[1].angle = beakMin
  time.sleep(1)
  kit.servo[1].angle = None

#Flügel senken

  kit.servo[3].angle = wingsMin
  time.sleep(1)
  kit.servo[3].angle = None
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
